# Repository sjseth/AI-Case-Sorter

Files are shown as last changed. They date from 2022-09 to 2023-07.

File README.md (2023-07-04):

# Important: This version of the project has been "retired"

## If you are thinking of starting on this project, please go to the latest version of the project CS7.1 Repo and start with the Instructions.pdf file. 

[CS7.1 Repo](https://github.com/sjseth/AI-Case-Sorter-CS7.1)

[CS7.1 Instructions](https://github.com/sjseth/AI-Case-Sorter-CS7.1/blob/12b74c1f0a16aa015d7ec6fccc47490c912a801d/Instructions.pdf)

# 
#

# AI-Case-Sorter ARCHIVE
This project contains the assets and resources for creating the AI Case sorter project as seen at: https://youtu.be/KBhd5qHZM7I

# Build Videos
[Sorter Construction Part 1][costruciotn1]

[Sorter Construction Part 2][costruciotn2]

[Sorter Construction Part 3][costruciotn3]

[Sorter Construcion Part 4][costruciotn4]

# CS7
[CS7 Concept Video][CS7-Concept]

[CS7 version update video][CS7-accouncement]

# Mods

[Strip-light Mod][light_mod]

[308 shell plate (requires CS7 "Tall" lid)][308_mod]

# Software
The software for this project can be found at: https://www.reloadingrecipes.com/

[Primer size sorting software update video][primer_update]

[costruciotn1]: <https://youtu.be/-Nw5cI27Rd8>
[costruciotn2]: <https://youtu.be/JH8qHSnzCFk>
[costruciotn3]: <https://youtu.be/LoM94kZkPA0>
[costruciotn4]: <https://youtu.be/fzv0i5LFrfs>

[CS7-Concept]: <https://youtu.be/BHhbmp4SDM4>
[CS7-accouncement]: <https://youtu.be/GTHugpKRd10>

[light_mod]: <https://youtu.be/j714uOy7tMQ>
[308_mod]: <https://youtu.be/jFpyLU6bnjw>

[primer_update]: <https://youtu.be/vlp6HSuLg_o>

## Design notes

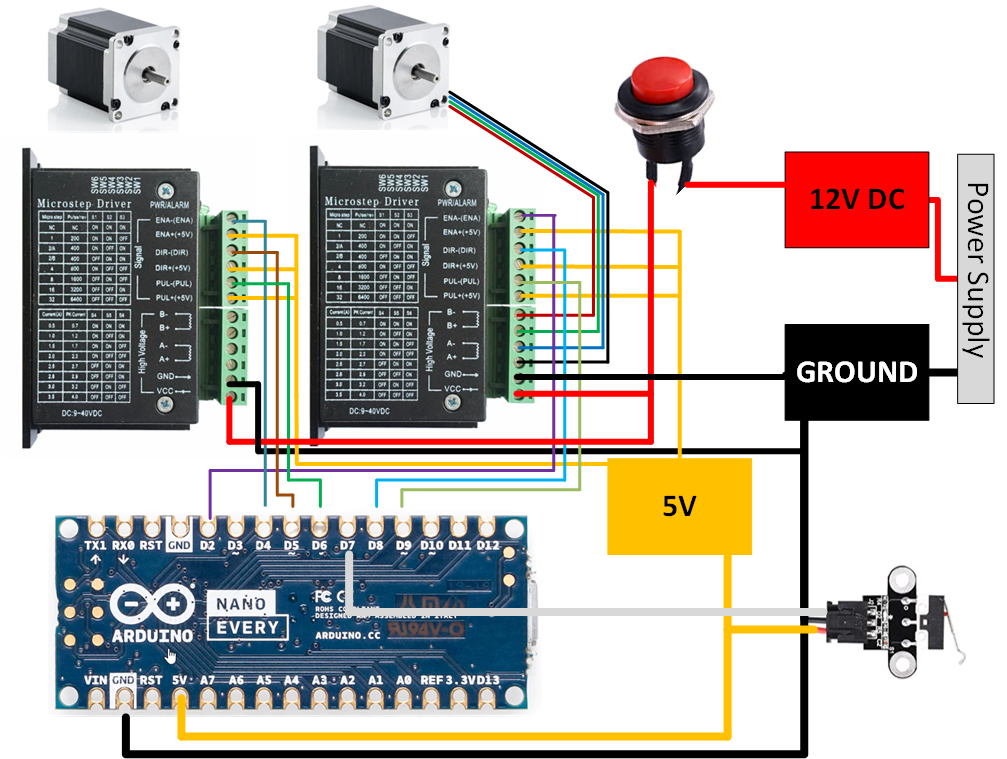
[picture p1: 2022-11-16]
Arduino/Case_Sorter_Schematic.png

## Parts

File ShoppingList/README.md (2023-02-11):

# AI-Case-Sorter

(2) [Nema17 Stepper Motors 1.5A](https://www.amazon.com/STEPPERONLINE-Stepper-63-74oz-Connector-Extruder/dp/B07LF898KN)

(1) [Arduino Nano](https://www.amazon.com/DWEII-ATmega328P-Compatible-Arduino-Unsoldered/dp/B09VKTPPZR)

(2) [TB6600 Stepper Controllers](https://www.amazon.com/UsongShine-Stepper-Controller-Arduino-Printer/dp/B07HHS14VQ)

(1) [ELP VGA Super Mini VGA USB Camera Module 100deg](https://www.amazon.com/dp/B01DRG250Q)

(1) [White LED String Light](https://www.amazon.com/Waterproof-Operated-Decoration-Christmas-Holiday/dp/B01837ULSC)
OR
(1) [White 4000k LED Strip Light (BETTER)](https://www.amazon.com/gp/product/B08X1LK54Z)

(1) [4K ohm resistor](https://www.amazon.com/dp/B0185FHL30)

(1) [Threaded Insert Kit](https://www.amazon.com/Hilitchi-Threaded-Embedment-Printing-Assortment/dp/B08Z86Z85R)

Alternatively, you can use buy just the sized you need:
-  [m3x6x5](https://www.amazon.com/Hilitchi-Threaded-Embedment-Printing-Assortment/dp/B08Z89R4HP)
-  [m5x8x7](https://www.amazon.com/Hilitchi-Threaded-Embedment-Printing-Assortment/dp/B08Z89Q6F7)

(1) [M3 M4 M5 flat head kit](https://www.amazon.com/gp/product/B077ZWV6T2)
or: 
- (4) m3x12 flat head
- (8) m3x16 flat head
- (4) m4x20 hex socket 
- (4) M3x16 hex socket

(1) [M6 hex nut kit ](https://www.amazon.com/M6-1-0-Stainless-Thread-Bright-Finish/dp/B08Y8PV88V/)
 
(1) [5mm Flange Shaft Coupling](https://www.amazon.com/gp/product/B07L1FMBBC)
(1) [Assorted spring kit](https://www.amazon.com/gp/product/B076XKY3JM)
or: 
- (1) 5.55x25.4 extension spring
- (1) 9.1x34.9 compression spring

(1) [Micro Limit Switch (homing sensor)](https://www.amazon.com/gp/product/B07PCN6T6F)

(1) [12v 5amp Power Supply](https://www.amazon.com/gp/product/B01GEA8PQA)

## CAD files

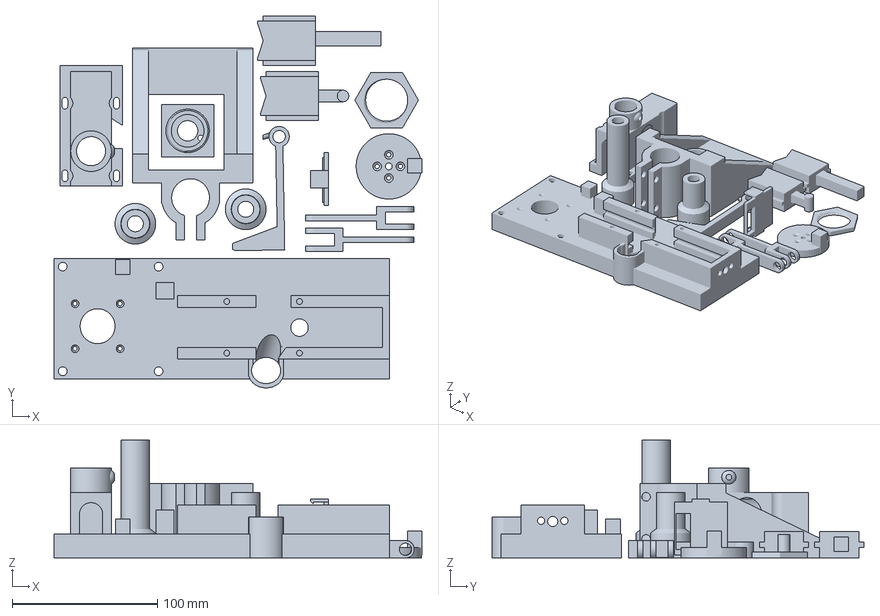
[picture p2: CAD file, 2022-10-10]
3D Printed Modules/1 - Classifier/CS6/CFFFP_CS6_Complete.3mf
253.3 x 256.0 x 81.0 mm

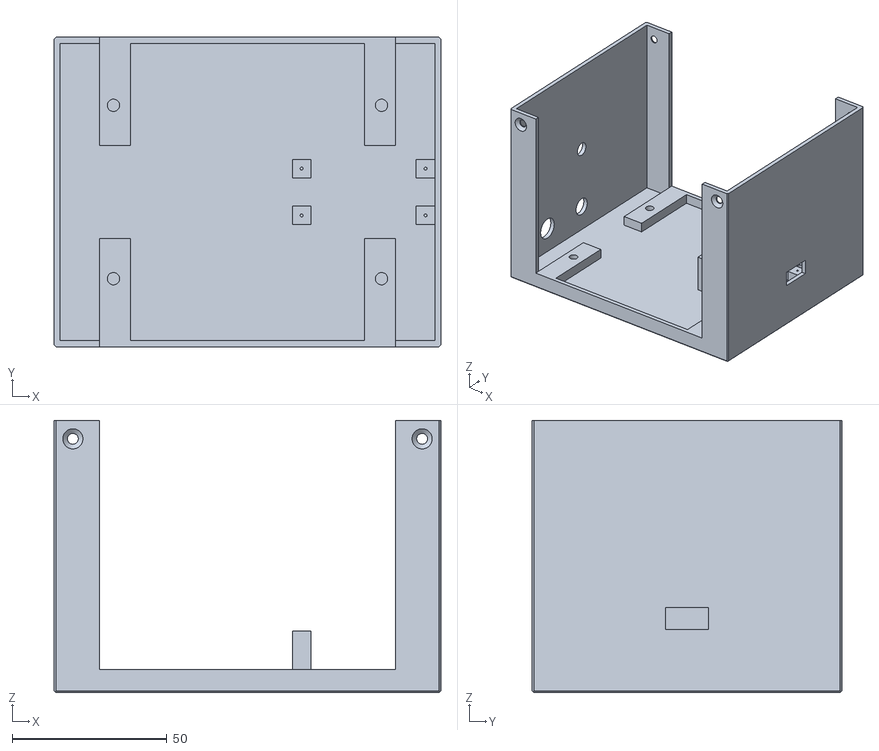
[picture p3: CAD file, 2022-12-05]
3D Printed Modules/3 - Electronics Housing/Experimental/CS7 - Nano + TB6600 Electronics Main.stl
125.0 x 100.0 x 88.0

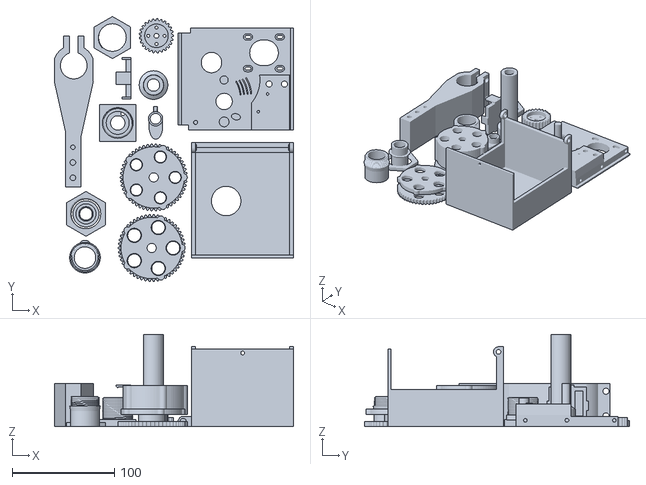
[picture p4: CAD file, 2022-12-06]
3D Printed Modules/1 - Classifier/CS7/CS7_Classifier_Complete.stl
234.0 x 259.0 x 90.0

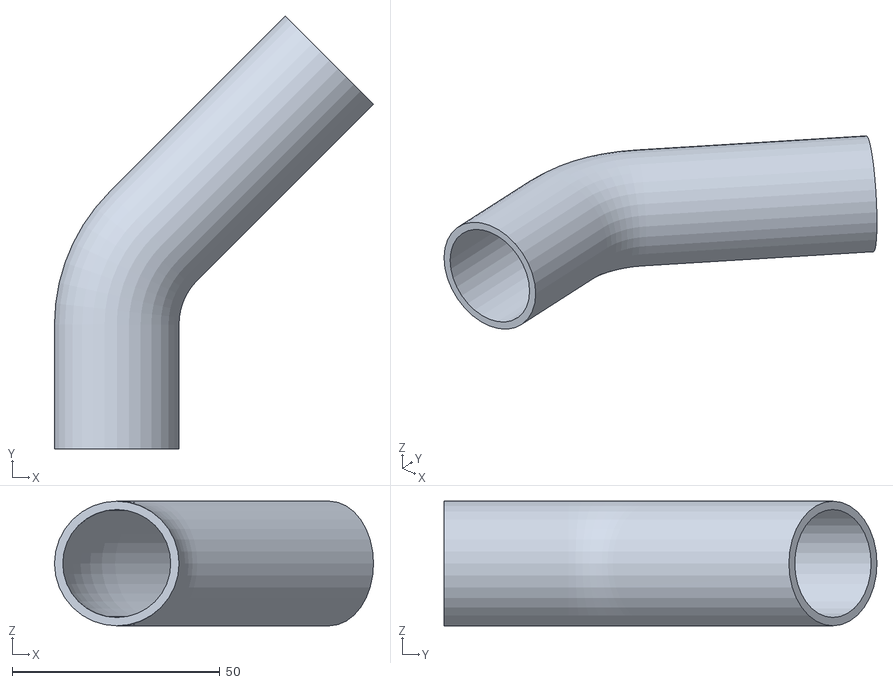
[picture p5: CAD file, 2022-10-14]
3D Printed Modules/2 - Sorter/FeedPipeMain.stl
76.8 x 104.2 x 30.0

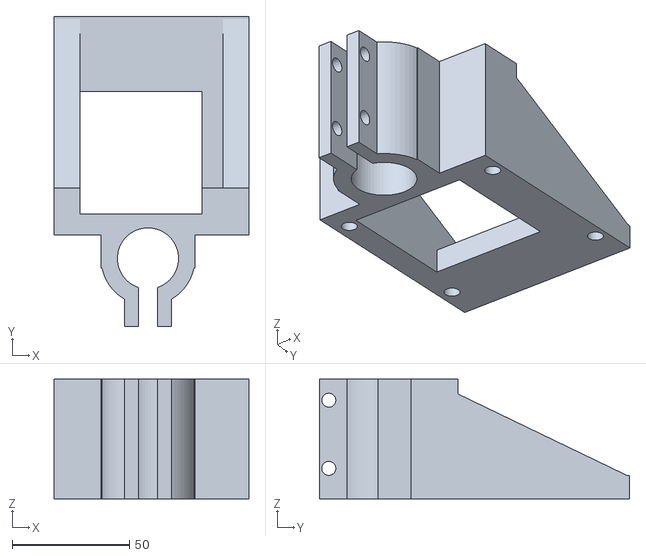
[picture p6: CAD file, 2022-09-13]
3D Printed Modules/1 - Classifier/CS6/CS6_MainBodyPoleMount.stl
83.0 x 132.0 x 51.0

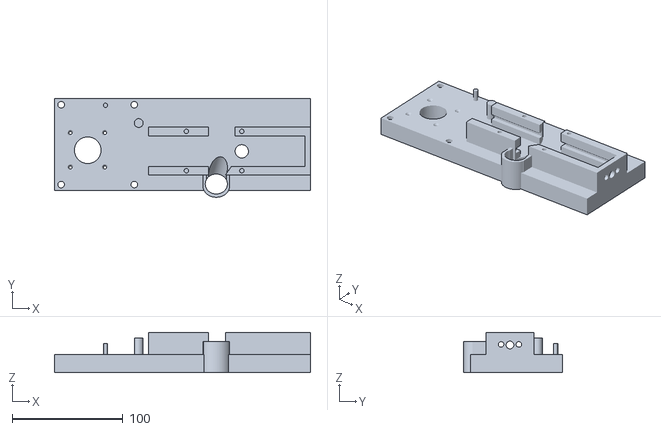
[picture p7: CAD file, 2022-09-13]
3D Printed Modules/1 - Classifier/CS6/CS6_MachineMainBody.stl
231.0 x 89.0 x 36.5

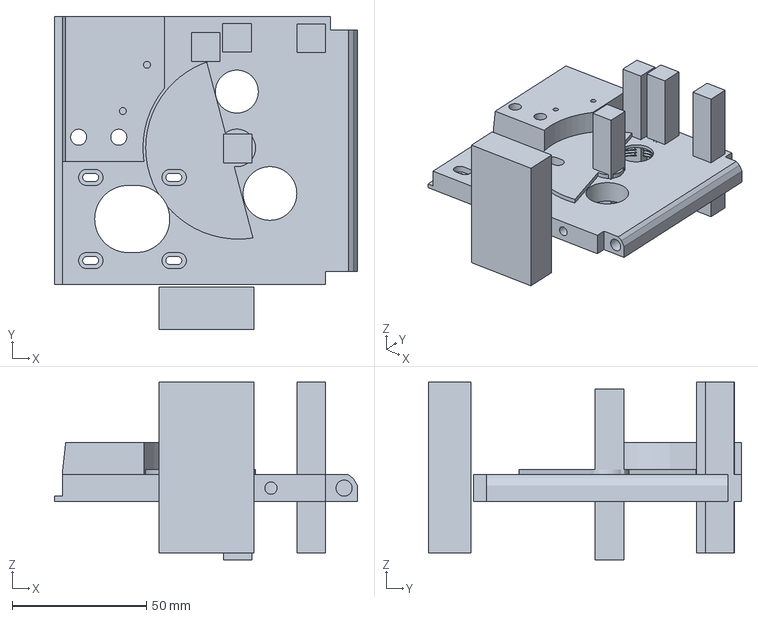
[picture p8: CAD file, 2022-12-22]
3D Printed Modules/0 - Camera/Experimental/CFFFP_CS7 - Sorter Base Exp.3mf
113.0 x 116.7 x 66.3 mm
CS7 - Sorter Base Exp.stl
CS7 - Tension Cam Extended w oRing.stl

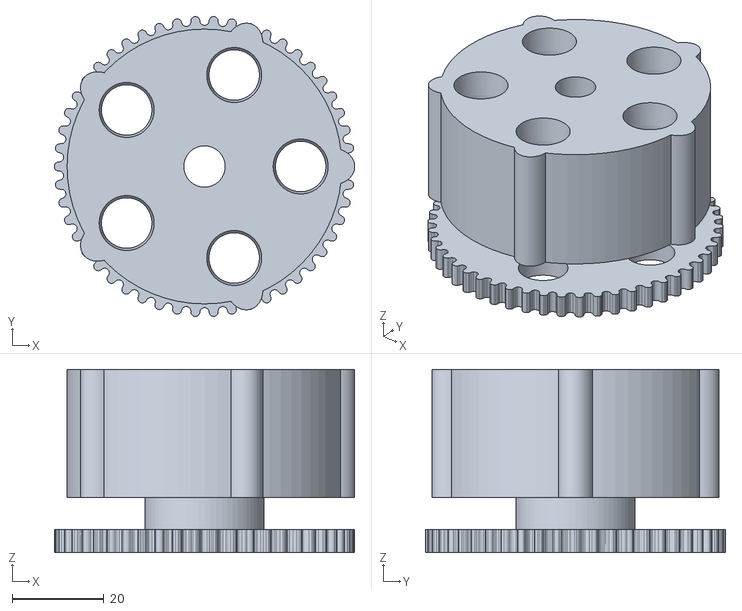
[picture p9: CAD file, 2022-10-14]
3D Printed Modules/1 - Classifier/CS7/Caliber Specific Parts/223-556/CS7_223-556-IndexWheel.stl
65.6 x 65.5 x 40.0

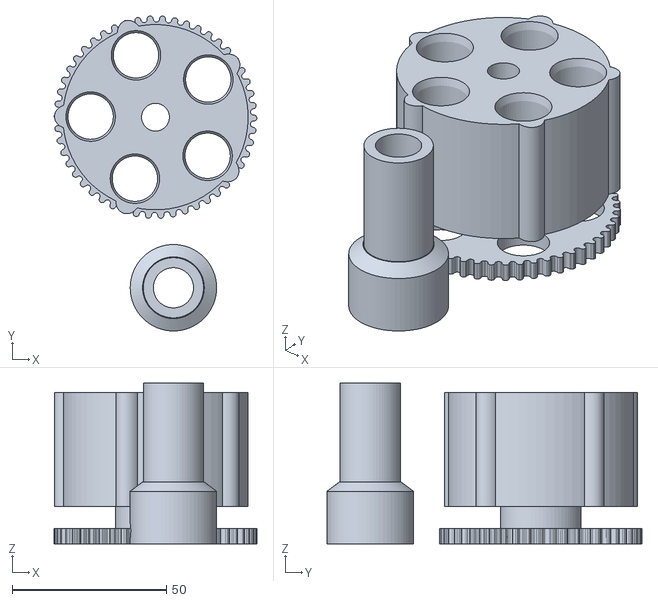
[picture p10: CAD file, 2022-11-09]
3D Printed Modules/1 - Classifier/CS7/Caliber Specific Parts/308/CS7-308-Conversion.stl
65.6 x 102.0 x 52.0

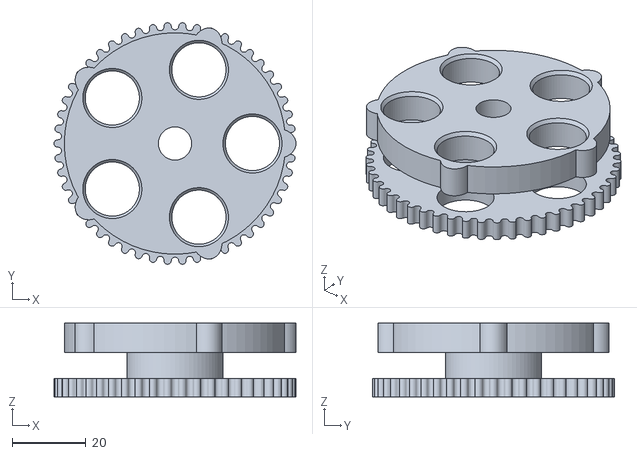
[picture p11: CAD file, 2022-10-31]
3D Printed Modules/1 - Classifier/CS7/Caliber Specific Parts/45AUTO/CS7-Wheel-45AUTO.stl
65.6 x 65.5 x 20.0

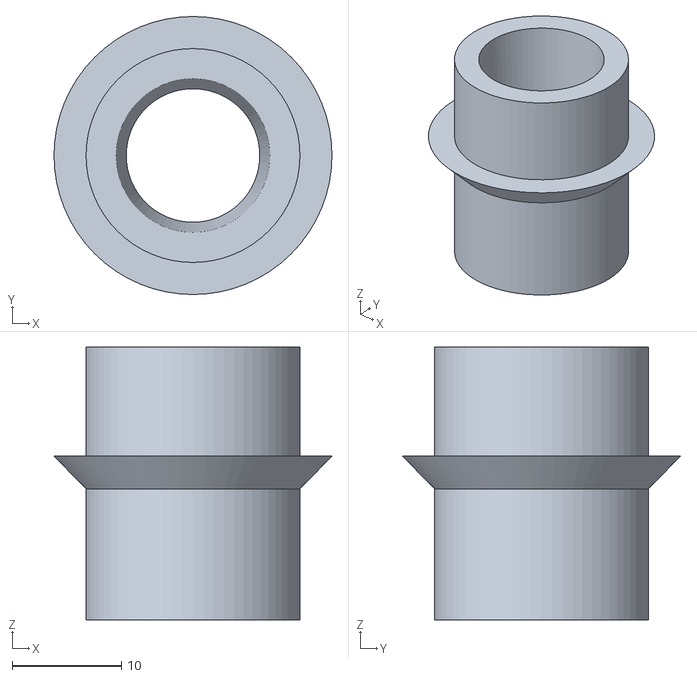
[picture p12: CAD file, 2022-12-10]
3D Printed Modules/1 - Classifier/CS7/Caliber Specific Parts/9mm/CS7 - 9mm Drop Nozzle.stl
25.5 x 25.5 x 25.0

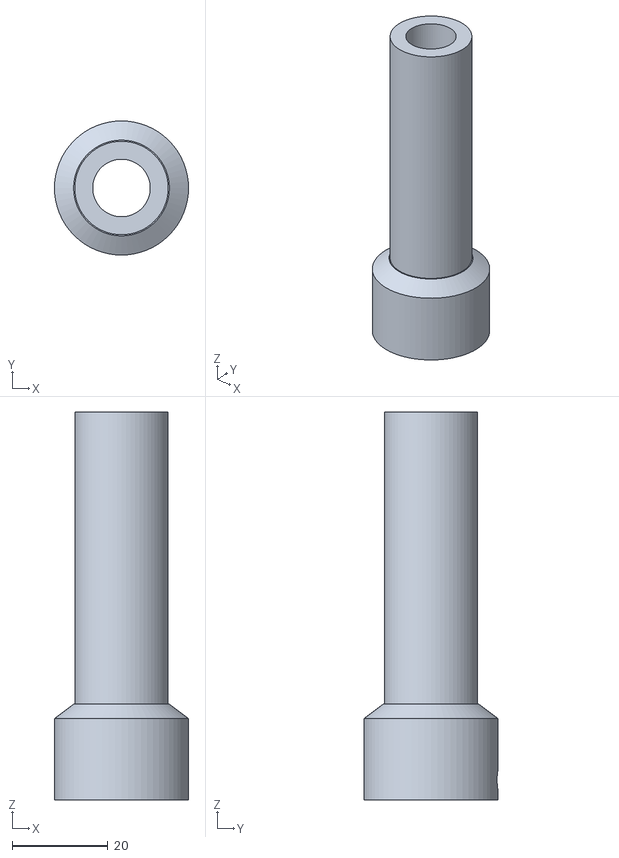
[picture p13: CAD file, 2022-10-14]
3D Printed Modules/1 - Classifier/CS7/Caliber Specific Parts/CS7_FeedNozzle.stl
28.0 x 28.0 x 81.0

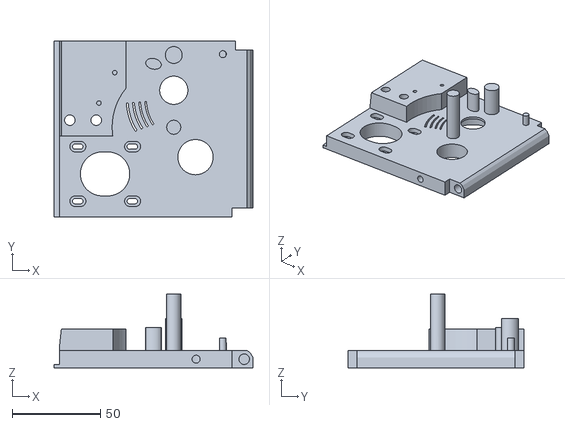
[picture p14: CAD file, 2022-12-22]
3D Printed Modules/1 - Classifier/CS7/Experimental/AirShield/CS7_1 Blackbox Base.stl
113.0 x 100.0 x 42.0

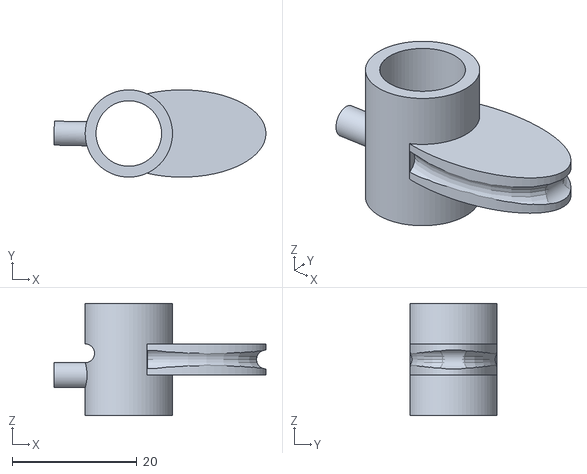
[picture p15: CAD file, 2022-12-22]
3D Printed Modules/1 - Classifier/CS7/Experimental/CS7 - Tension Cam Extended w oRing.stl
34.0 x 14.0 x 18.0

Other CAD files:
3D Printed Modules/1 - Classifier/CS6/CS6_Complete.stl
3D Printed Modules/2 - Sorter/CS5/CS5_PVC_PLATE.stl
3D Printed Modules/2 - Sorter/CS6/Sorter_Arm.stl
3D Printed Modules/2 - Sorter/CS7/27_5mm Mount -IronPipe/Sorter Minimal Mount_27mm.stl
3D Printed Modules/0 - Camera/CS5_CameraModule_lid.stl
3D Printed Modules/0 - Camera/CS5_LightRing.stl
3D Printed Modules/0 - Camera/CS6_CameraModule_Body.stl
3D Printed Modules/0 - Camera/CS7_Camera_Nut.stl
3D Printed Modules/0 - Camera/Experimental/CS7 Camera v2.stl
3D Printed Modules/0 - Camera/Experimental/CS7_1_BlackboxBase.3mf
3D Printed Modules/1 - Classifier/CS6/CS6_223FeedPiston.stl
3D Printed Modules/1 - Classifier/CS6/CS6_9mmFeedFunnel.stl
3D Printed Modules/1 - Classifier/CS6/CS6_Con-rod.stl
3D Printed Modules/1 - Classifier/CS6/CS6_Ejector.stl
3D Printed Modules/1 - Classifier/CS6/CS6_FeedBed_ShortVersion.stl
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

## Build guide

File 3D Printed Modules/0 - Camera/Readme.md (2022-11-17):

# Camera Module
The Camera Module consists of 4 parts:

## The Camera
The cameras is a USB camera module with a 100 degree lense, be sure you purchase the 100 degree lense variant as other lenses have not been tested and this will reduce compatability of AI training sets between your build and other peoples. 

[Source from Amazon.com][Amazon-link]

[Source from Ali Express][Aliexpress-link]

## Camera Body 
Print with supports only touching base and support overhange angle at 80 degrees. This will prevent supports from getting in the threads. 
If using Cura Slicer, use these support settings: 

* Support Structure: Normal,  
* Support Placement: Touching Buildplate, 
* Support Overhang Angle: 80.0, 
* Support Wall Line count: 0

## Camera Nut
This should be placed flat on the build plate and printed without supports. 

## Camera Module Lid
Should be printed with the flat part down with supports on to suport the clips. 
If you are getting breakage at the clips or poor layer adhesion, you can print this part on its side with supports for greater strength. 
Recommend use of PLA+ for this part. 

[Amazon-link]: <https://www.amazon.com/dp/B01DRG250Qdcwxa>

[Aliexpress-link]: <https://www.aliexpress.com/item/4000614474904.html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"sku_id"%3A"10000004016284977"%7D&pdp_npi=2%40dis%21NOK%21263.94%21250.77%21%21%2192.79%21%21%402101e9d316664697050524419e75a3%2110000004016284977%21sea&curPageLogUid=ZHqutjEPQrzU>

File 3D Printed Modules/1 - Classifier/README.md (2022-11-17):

# Classifier
The classifier takes in brass via the feed nozzel, Imaged it using the camera module and drops it out the drop nozzle. 

It is reccomended that the classifier is built as the second module of the build so that you can build your training set while the sorting module is printing. 

It is reccomended that anyone starting with this project does so using the CS7 build

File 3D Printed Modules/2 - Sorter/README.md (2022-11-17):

# Sorter
The sorter rotates a feed pipe to sort cases into one of many bins by rotating the to the appropriate bin prior to the classifier dropping the case.

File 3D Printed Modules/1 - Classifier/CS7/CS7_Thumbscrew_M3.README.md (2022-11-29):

### Thumbscrew cap created by user: anticolon. 

This is a cap which can be glued to a m3 screw and used as a thumbscrew to replace the existing m3 screw which holds the lid on.

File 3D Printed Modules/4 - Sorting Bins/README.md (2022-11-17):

# Sorting Bins

The sorting bin has an additional spot to hold a slip of paper or cardstock to label the contents of your bin and a hole for hanging the bins that is also helpful in grabbing and moving them about. 

The label holder is sized appropriately to accept a [standard microscope][amazon_miscroscope_slides] slide to keep your labels from getting dirty. 

[amazon_miscroscope_slides]: <https://www.amazon.com/gp/product/B0747R2M26/ref=ppx_yo_dt_b_search_asin_title?ie=UTF8&th=1>

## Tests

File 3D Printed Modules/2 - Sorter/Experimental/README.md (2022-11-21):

# Experimental
Stuff in this folder is in the process of being tested/refined. 

### Sorter Minimal Design
This design eliminates the sorter plate and piping. It features an adjustable motor/sorter arm mount. 
Recommend printing in PLA+ at layer height of .24mm with infill no less than 15%. Supports are required and recommendation is support overhang angle of 80 degrees. 

* SorterMinimalDesign (Includes both sides of mount)
* SorterMinimalDesign_MotorSide (the side which motor attaches to)
* SorterMinimalDesign_PoleSide (the side which attaches to the pole)

### Here is an example of what it looks like:
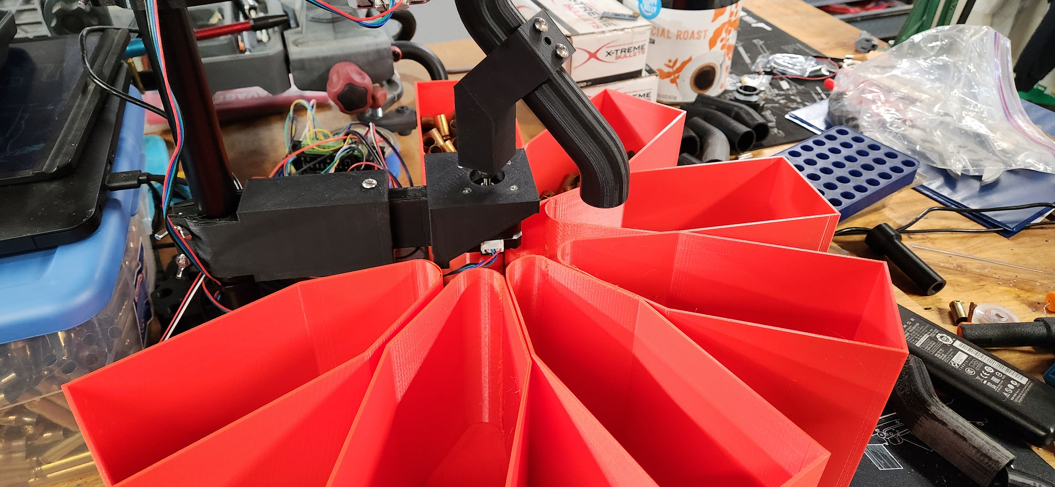
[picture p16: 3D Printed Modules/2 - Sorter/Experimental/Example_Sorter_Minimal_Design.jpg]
SorterMinimalDesign


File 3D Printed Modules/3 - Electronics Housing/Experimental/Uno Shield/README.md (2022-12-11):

### Electronics housing for Arduino Uno with motor shield

Here is the parts list for this enclosure

* [40mm Fan](https://www.amazon.com/dp/B07CH6YC32)
* [CNC Shield Expansion Board V3.0 +UNO R3 Board + A4988 Stepper](https://www.amazon.com/dp/B06XHKSVTG)
* [5.5 x 2.5mm DC-099 DC Jack](https://www.amazon.com/outstanding-5-Pack-Threaded-Connector-Adapter/dp/B07C4F7BP5)
* [SPST Latching Type Push Button](https://www.amazon.com/gp/product/B06XF6PT9L)

The code for the Arduino Uno with motor shield is here:

[Uno with MotorShield Code ](../../../../Arduino/case_sorter_CS7_UNOSHIELD)

# Other Resources

* [Link to CNC Shield Manual](https://www.zyltech.com/arduino-cnc-shield-instructions/)
* [2.54mm Connector Kit](https://www.amazon.com/Glarks-Connector-Housing-Compatible-Assortment/dp/B07CTHCG5T)
* [2.54 Crimper tool](https://www.amazon.com/gp/product/B088NQV8Z3)

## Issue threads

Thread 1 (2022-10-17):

Camera module

xaybiz, 2022-10-17:
Hi
First of all thank you for sharing this fun project!

I have a question regarding the camera module. The seller on Amazon doesn’t seem to ship to Europe (or at least to my country). Do you know another link from for example Aliexpress for a camera that would work? I’m having trouble finding the correct size.

Kokken76, 2022-10-22:
This seems to be the same
https://www.aliexpress.com/item/4000614474904.html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"sku_id"%3A"10000004016284977"%7D&pdp_npi=2%40dis%21NOK%21263.94%21250.77%21%21%2192.79%21%21%402101e9d316664697050524419e75a3%2110000004016284977%21sea&curPageLogUid=ZHqutjEPQrzU

sjseth, 2022-10-23:
Yes, it appears to be...and at a lower price if you are willing to wait

Sent from my Verizon, Samsung Galaxy smartphone

-------- Original message --------
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

xaybiz, 2022-10-23:
Thanks! I actually found and bought it yesterday. I was going to update here but you beat me to it.

It’s either waiting 1-2 months for this camera or modifying the camera housing to fit other circuit board size. I was being lazy this time since I’m not in a hurry.

Closed 2022-11-29.

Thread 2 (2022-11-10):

Separate Objects within .STL files

osteth, 2022-11-10:
Hey! This projects if very cool. I recently ran into an issue printing out the CS7 base.
Within the following file:
[AI-Case-Sorter](https://github.com/sjseth/AI-Case-Sorter)/[3dModels](https://github.com/sjseth/AI-Case-
Sorter/tree/main/3dModels)/[CS7](https://github.com/sjseth/AI-Case-Sorter/tree/main/3dModels/CS7)/CS7_BlackBox_Base_wSensor.stl

The drop nozzle is floating above the build plate so that it is printed in mid-air causing the print to fail.
This specific issue highlights the fact that multiple .stl files have multiple parts combined in the same file. This makes it very difficult to orient and print each part appropriately as well as causing difficulty reprinting any combined part that fails to print properly.

If you are able to break them out in your cad program into individul components per .stl file It would be appreciated. I am currenty addressing the issue adding negative build volume in prusa slicer to make the other parts not print and its not a great work arround.

sjseth, 2022-11-11:
Thanks for letting me know. I will have a look and fix.

________________________________
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

sjseth, 2022-11-11:
Hi Seth,

I have updated the models to fix the issue. Actually I removed that model as it wasn't supposed to go to the repo.

The latest version of the base is here:
https://github.com/sjseth/AI-Case-Sorter/blob/main/3dModels/CS7/CS7_BlackBox_Base.stl

Also the nozzle is separate now as well:
https://github.com/sjseth/AI-Case-Sorter/blob/main/3dModels/CS7/CS7_9mm_nozzle.stl

Cheers!

________________________________
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

osteth, 2022-11-16:
No problem,  I did have a similar but different issue with
https://github.com/sjseth/AI-Case-Sorter/blob/main/3dModels/CS7/CS7_CameraParts.stl
I wanted to print the camera backing with support for the clips. but I couldn't manage to remove the support material without destroying the threads of the other two parts. wasn't a particularly large hurdle. I just turned on supports and placed a support exclusion on the treaded parts and that got me there. but breaking them apart could be useful.

Closed 2022-11-16.

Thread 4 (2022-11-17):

Electronics Enclosure Lid??

osteth, 2022-11-17:
Is there a lid for the electronics enclosure? I couldn't find one.

sjseth, 2022-11-17:
Currently there is no lid. The enclosure needs to be redesigned. It has several issues which need to be addressed. I have a few experiments to complete with other controllers before I spend more time on the enclosure.  Not sure if I want to stay with the tb6600 as there are better options out there

Sent from my Verizon, Samsung Galaxy smartphone

-------- Original message --------
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

osteth, 2022-11-17:
ok cool.
It might be worth taking a look at something like these low cost modules. they would significantly reduce the build cost if they are sufficient.
https://www.amazon.com/Expansion-Stepper-Drivers-Arduino-Printer/dp/B07LH5XTCL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

Closed 2022-11-22.

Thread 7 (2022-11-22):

Motor Driver dimensional tollerances.

osteth, 2022-11-22:
I got in a motor driver today that is too large for the enclosure. I purchased from the provided link. but it appears that they don't have terribly tight tolerances on the heat sink extrusions.

The ones I received measured out to 118.5mm so they will not fit in between the enclosure walls. I just wanted to make a note of it because there appears to be some variability even from the same vendor.

sjseth, 2022-11-29:
Ok, thanks for the info. I am leaving this open for now as I am working on a new electronics package / enclosure which I think will be much better than the current existing setup which uses the tb6600.

osteth, 2022-11-30:
Now I see where the package size issue I am having came from. They sent me DM556 drivers instead of tb6600 even though I ordered off the tb6600 link in the shopping list.

Alphadawg0024, 2023-02-27:
Do you have an updated link to the Discord server. Jumping into this project but the Discord link expired

sjseth, 2023-02-27:
Please email me directly for that.  I don't want to publish links here.

Email is in the about page here:

***@***.***/about

________________________________
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

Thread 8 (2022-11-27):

CS7_Camera_Nut.stl size

Mograthi, 2022-11-27:
The CS7_Camera_Nut.stl is importing into slicers as a giant object 379.6 x 438.3 x 40 mm

osteth, 2022-11-28:
That one is on me. I tried to isolate the nut from the rest of the parts without the original cad file and something went wrong apparently ( I am assuming that it was a unit conversion issue)
Please use this file until I can figure it out.
https://github.com/sjseth/AI-Case-Sorter/blob/a3689c34340b883cd53d27106b8b8bb5844e6180/3dModels/CS7/CS7_CameraParts.stl5

osteth, 2022-11-28:
The issue should be rectified in my pull request. (https://github.com/sjseth/AI-Case-Sorter/pull/9)
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

sjseth, 2022-11-29:
Thanks for the quick fix.  Verified that the issue has been resolved.

Closed 2022-11-29.

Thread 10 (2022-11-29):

Thumbscrew for the lid and droptube.

anticolon, 2022-11-29:
Hey Seth, just found your project the other day on youtube and was thrilled as i've been thinking of designing something along these lines for a while now. I'm printing your design as we speak and have already ordered most of the stuff needed. So big thanks for sharing this project!

Now, to my idea for improvement, in other projects with screws to secure stuff, I've seen people using a hexbolt (screw) and then printing a small thumbpart that fits over the head. This is quite secure when fitted with hotglue. This would minimize the need for tools when doing caliber change.

Best regards
Karl

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

anticolon, 2022-11-29:
I'll try to add an STL for a similar that I just made.

osteth, 2022-11-29:
The general workflow for making changes to a repo is to make a fork,
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
Then make a branch inside of your fork. (shown using github desktop client https://desktop.github.com/)
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
Then make and commit your changes to your branch
Finally, generate a pull request to allow for them to be reviewed and merged into main.
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

If all else fails you can change the file extension from .stl to .png and upload them in a comment here and I can generate a merge request.

sjseth, 2022-11-29:
Thanks anitcolon for the idea and Seth for the guidance.  The pull request has been merged to the branch and in addition I added a readme file for how the screw is supposed to be used since it requires additional gluing.

anticolon, 2022-11-29:
Turns out, atleast when i print them, they are pressfit. No glueing required.

anticolon, 2022-11-29:
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

Closed 2022-11-29.

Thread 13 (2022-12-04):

Add countersink to motormount on CS7 classifier base.

anticolon, 2022-12-04:
When mounting the motor I needed to drill out some material to countersink the screws so that the indexwheel could move freely.
Would be nice to have it in the model.

sjseth, 2022-12-05:
I am working on this one. thinking of recessing them all and using cap screws. Doing some experiments.

sjseth, 2022-12-06:
Thanks. I have recessed 3mm and tested it and it works with both standard and cap m3 screws.

anticolon, 2022-12-06:
Looks good!

Closed 2022-12-06.

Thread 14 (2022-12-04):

CS7 Classifier drive gear catches indexwheel when rotating.

anticolon, 2022-12-04:
Had to remove some material from the 9mm indexwheel so that the drivegear wouldn't catch when rotating. Maybe the drivegear doesn't have to be that tall, and thus removing the issue?

sjseth, 2022-12-05:
Ok, I have updated the drive gear to shorten it which resolves this issue. Thanks!

Closed 2022-12-05.

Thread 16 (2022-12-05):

Feed Adapter compatible with BF556 Feeder design.

anticolon, 2022-12-05:
Hi Seth,

Could you make a experimental feed adapter with innerdiameter of 16,5mm and make the top lower by 6mm? This would make it plug & play with the LEE APP droptubes in the excellent feeder that BF556 has designed.
https://github.com/BF556/Feeder

Would be much appreciated!

sjseth, 2022-12-05:
Added to the Experimental folder in classifier

anticolon, 2022-12-06:
Thank you! Will print later today for testing.

anticolon, 2022-12-06:
Printed it, and i think it needs 0,5mm more, so could you update it to 17mm inner diameter. Lengthwise it's perfect.

Closed 2022-12-05.

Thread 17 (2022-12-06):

BF556 feed adapter adjustment

anticolon, 2022-12-06:
Don't know if this is the right way to go about changes to a closed issue, but here i go. Correct me if I should have done it some other way. :)

Printed it, and i think it needs 0,5mm more, so could you update it to 17mm inner diameter. Lengthwise it's perfect.

Originally posted by @anticolon in https://github.com/sjseth/AI-Case-Sorter/issues/16#issuecomment-1339792251_

sjseth, 2022-12-06:
I am guessing it is probably related to shrinkage. Can you measure your printed item to see if what the ID is?
If it is not 16.5, you might try scaling it up by 1 or 2 percent.

If it did print out exactly at 16.5mm and is too small, I am happy to increase the ID to 17.

________________________________
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

sjseth, 2022-12-07:
Thanks for the update Karl. I have no problem making it bigger and I don't think .5mm will have much effect anyhow, but the original requestor requested it to be  16.5 so I didn't want to mess him up either.  I suspect that for this application 16.5 would be a very tight fit as well as 17mm so I will go ahead and update it.

________________________________
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

sjseth, 2022-12-07:
Sorry, just realized that Karl and Anticolon are 1 in the same... I have updated the part.

anticolon, 2022-12-07:
Hehe, I just added my name to the profile, thought it would be nicer that way. Thanks for updating, I'll print a new one tomorrow and get back to you. Midnight here in Sweden. 😀

anticolon, 2022-12-09:
Printed and verified, works perfectly now that you made the ID 17mm.

Closed 2022-12-07.

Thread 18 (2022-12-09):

Sorter Plate Too Large for My Printer

BigTJohn, 2022-12-09:
When I import the sorter plate.stl into Cura, it says the dimension is too late for my build area. I have an Ender 3 S1 Pro with a build area of 220x220x270. Was sure it would fit. Is there a smaller dimension I can use or do I try to make a wooden sorter plate?

anticolon, 2022-12-09:
That's not right, I'm not used to Cura, but did you import the model with the correct settings. I believe it should be imported with metrics (mm) setting.

BigTJohn, 2022-12-09:
I’m sure I just downloaded the file from SJSETH then just imported it to CURA. I did the same to all the rest of the files and they are good. Some long print times but very good quality. I have only the outer greyed out margins on the print preview left but I don’t think I can use that area. I was sure the file would be just fine however it just is too big for the printer. I don’t know what the physical measurement of the Sorter Plate is, but it would seem it would fit easily
Thanks for getting back, John

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

sjseth, 2022-12-09:
It may be that Cura is accounting for the skirt or brim. If you set the build plate adhesion type to none, it should be fine for your bed size of 220

BigTJohn, 2022-12-11:
This could be the case however, the other items so far have been downloaded and imported to cura, sliced and they print very well. How big is the sorter plate in mm? It just does not make sense it is so large. On your video, it seems no larger than 150-160 mm across. But that’s just a guess on my part. I will try to get it to download again and see what happens.
Thanks, John.

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

sjseth, 2022-12-11:
It is 200mm diameter. There is a minimal sorter 3d model which can be seen in my  latest video which is in the experimental folder. It had a much smaller print area requirement and may work better for you.

https://youtu.be/uEW3m3bBLPA

Sent from my Verizon, Samsung Galaxy smartphone

BigTJohn, 2022-12-11:
You were correct, it was the skirt/brim. Changed that to "none" and it is printing merrily away. Should be done in another 16 hrs or so.
The link listed in the recent video for the taller lid does not come up. I get a "404" not found message and I do not see the tall lid in the print files.
Many thanks for this project, it is proving quite the fun challenge. So far the electronic side coming together. I see the new electronic box (are files available yet?) uses an Arduino UNO instead of the Nano.  Good thing as I have two of them. Now waiting for the motor shield and camera to come in.

sjseth, 2022-12-11:
The tall lid is now the normal lid

https://github.com/sjseth/AI-Case-Sorter/blob/main/3D%20Printed%20Modules/1%20-%20Classifier/CS7/CS7_Classifier_Lid.stl

The new electronics models and info is here:
https://github.com/sjseth/AI-Case-Sorter/tree/main/3D%20Printed%20Modules/3%20-%20Electronics%20Housing/Experimental/Uno%20Shield

Sent from my Verizon, Samsung Galaxy smartphone

-------- Original message --------
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

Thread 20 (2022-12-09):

Arduino Uno Shield Electrical Drawing

BrickSolid28, 2022-12-09:
Does anyone have a basic electrical drawing for the Uno with CNC backpack?  Even a basic picture of a working setup would help.  Are we using a 12V or 24V power source for the shield?  I'm assuming 12V as the specified fan is 12V.

sjseth, 2022-12-10:
I am releasing a video on it tomorrow. Stay tuned.
________________________________
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

sjseth, 2022-12-11:
Hopefully this has the information you need.  https://www.youtube.com/watch?v=uEW3m3bBLPA
Also you can find more info in the  Experimental->Uno Shield folder:

https://github.com/sjseth/AI-Case-Sorter/tree/main/3D%20Printed%20Modules/3%20-%20Electronics%20Housing/Experimental/Uno%20Shield

Closed 2022-12-11.

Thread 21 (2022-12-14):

New Sort Pipes

BigTJohn, 2022-12-14:
The New Sort Pipes, while they print great, I think only one of the non flared pipes is needed but they only print in pairs, one non flared and one flared. Since several flared pipes are needed (up to 10) I cannot seem to break out the pair of pipes for individual printing, Is there a method of doing so?
Thanks, John

sjseth, 2022-12-14:
If i understood you correctly, the pair of flared sort pipes with smaller ID were designed be used only for the moving arm where the flat ends butt together. It was a later design where I got rid of the all the other pipes as the two pipes together drop the brass straight down.

Sent from my Verizon, Samsung Galaxy smartphone

-------- Original message --------
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

BigTJohn, 2022-12-15:
So the newest iteration does not use the sorter plate or the 10 pipes from the plate to the bins. If I am understanding this correctly. So far this has been a very interesting journey. Can’t wait to get it finished.
I am assuming you have the .stl files locked and no one can do much if any changes. I have been able to resize a couple things, the bins and the sorter arm.
Thanks for doing this. It’s great!
John

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

sjseth, 2022-12-15:
You should be able to pull the stl file into almost any CAD program and make changes to it. I don't have the source for the files available at this point in time.

Sent from my Verizon, Samsung Galaxy smartphone

-------- Original message --------
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

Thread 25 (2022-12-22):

Arduino sketch

BigTJohn, 2022-12-22:
Me again. Finally got the camera with air shield to fit the black base. It required a bit of sanding and fitting but it is in place. Working on printing sort bins now. Two are in TPU and are maybe a bit too flexible but not terrible. I will do two more in PLA+ and most likely they will bw better suited.
The Arduino sketch is having a problem when I verify it.

//set feed speed. Values 1-100. Def 60

      if(input.startsWith("feedspeed:")){    RIGHT HERE it will fault the statement "a function-definition is not allowed here before "{" token

         input.replace("feedspeed:","");
         feedSpeed= input.toInt();
          Serial.print("ok\n");

I have tried to check why it's doing this but have been fruitless.
Also the stepper motor shield sketch is showing the TB9600 controllers, not the newer, smaller ones with the CNC shield. Does this make a difference in the operation of the Arduino/shield combo?
At least I'm getting closer and with the 3D prints about done it is actually looking much better. Still a ways to go but so far its been fun.

sjseth, 2022-12-22:
Can you tell me which sketch you were using?

Sent from my Verizon, Samsung Galaxy smartphone

-------- Original message --------
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

sjseth, 2022-12-22:
I just checked and compiled all 3 sketches from the repo and they all are working.  Not sure why you would see the error you are seeing. If you modified the sketch, it is possible you left out a closing bracket or semi colon.

In regards to the Arduino Uno sketch having references to tb6600, this is because this sketch is just an evolution of the previous cs7 sketch and I reused the variable names.  It is a good idea to update the variable names as it is a bit confusing.

BigTJohn, 2022-12-23:
Thanks for the quick reply. I haven’t changed the sketch but I will copy it again and see if something was lost in the copy. I would think it would be an easy thing to find, but I just do not see it.
Good idea about updating the naming things separately for each update in equipment. It’s nice to see everything working and I can pretty much follow on with it.
As far as the new sort pipes, I think just a slight change in the radius of the curves would make all the difference and allow 30.06 brass to pass. I just filed/sanded a little and I have the bigger brass going smoothly.
Have a great Christmas!!

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

BigTJohn, 2022-12-26:
I was using the latest sketch, however I had copied it a few times and it finally was correct and loaded into my Arduino. I don’t have the camera software downloaded yet but soon. I still have some 3D printing to do but it has been pretty chilly (well, for FL downright cold) the past few days but should be good later this week. I still have the case feeder to do so still bunch to do. Any idea how many cases a minute the sorter can do? I’m just trying to get int9o my mind and feeder plans what I should try and plan for as far as feeder capabilities.
Also here’s another thing that popped into my little brain, how much force is applied to the sorter platform (the bottom of the floor plate) when the first few cases fall from the feeder? It appears to take quite a hit until there are 5-6 cases in the feeder tube. Am I over thinking this? Should there be a few bends or maybe some brushes to slow the fall of the cases so the hit is not so hard?
Thanks, John

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

sjseth, 2022-12-26:
I think the max processing rate I have achieved was about 3 per second but that was with some of the setting changed and a few tweaks and a very powerful computer.  That said, I think a normal high-end max processing rate would be approximately 50-60rds per minute. There is a speed control in the run tab of the software to slow it down and I have to use that control or I outrun my feeder.

In regards to the force, it hasn't been a problem. If you are printing with pla or pla+ or something harder, it shouldn't be an issue. I don't have any dents in my base. But one thing to consider is that my drop tube actually has two bends in it so this may dampen it a bit. I think the most force is exhibited when you have a full tube of brass. Even then, with many thousands of of peices through the system, it haven't seen significant wear yet.

I use Black Jayo PLA+ for everything now days as it prints really well for me and doesn't crack/break. I get great adhesion at temp of 222C.
________________________________
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

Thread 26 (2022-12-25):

Notch or bend to make spring more secure?

anticolon, 2022-12-25:
Hey Seth,

Just got my sorter running on christmas day, still working out some kinks, I thought of some improvements that I'll post for your consideriation. I'll make an issue for each one.

Consider a notch or bend to make the spring more secure?
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

anticolon, 2022-12-29:
I put a 4mm hole there and put an insert with a screw.
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

BigTJohn, 2022-12-29:
I like your idea foe the spring attachment. I am using a silicon band to connect to the tension device. Your idea is much better and I’ll be doing this as well.
I drilled a hole for the Allen wrench to tighten the set screw on mine. I also used my Dremel to grind the motor shaft so the gear would sit lower as the flat section of the motor shaft would not let the gear go low enough.
This is proving to be a great project. I shoot mostly rife and the larger cases still fit the .308 sorter cylinder and lid. It will be a while before I can finish it up as my printer is taking a while to print and I just purchased it the end of November. So getting everything setup and learning the printer has been a journey as well.  So far, it has been pretty fun.
John...
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

sjseth, 2022-12-30:
I like this idea as well.  I am currently putting together a bunch of changes and combining them in a  7.1 folder.  I think I may use this idea though after adding the notches on both posts, the spring stays put pretty well. I have also redesigned the tension cam a bit as it now has a groove for an oring around it which gives it better gripping power on the case and also less noise as it slips through to the next cartridge.

sjseth, 2022-12-30:
John, the new gear is nearly half the height and should solve that interference issue. It is available now in the classifier folder

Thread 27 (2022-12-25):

Hole for limitswitch cable routing.

anticolon, 2022-12-25:
Hey Seth,

Consider adding a hole somewhere around here to route the cables from limitswitch, that way we could tie it togehter with the cable coming from the camera and link up with the cable from the motor and have a neat looking cable management. :-)

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

Best regards
Karl

anticolon, 2022-12-29:
I added a hole and also a groove at the motor to be able to torque the motorcoupler in the right height.
Should i fork and add this to the project? (there is still the thread for the camera.
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

sjseth, 2023-02-13:
Hi Karl,

Just wanted to let you know that I have created a Discord server for this project and if you are interested in joining, it would probably be a better place to get support and bounce ideas around with the community. I am in the process of inviting those who I know have already completed or are in the process of building this project.

Here is the link to join if you are interested:

https://discord.gg/HaUTpQhV<https://na01.safelinks.protection.outlook.com/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>

Cheers!

Seth
________________________________
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

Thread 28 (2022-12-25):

Notch or bend to make spring more secure

anticolon, 2022-12-25:
Hey Seth,

As per the other issue posted on the need for a notch or something that makes the spring more secure when running the classifier.

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

Best regards
Karl

sjseth, 2022-12-25:
Good point. Hasn't been an issue for me but wouldn't hurt to have a notch in both posts probably

Sent from my Verizon, Samsung Galaxy smartphone

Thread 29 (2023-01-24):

AI sorter download and run

BigTJohn, 2023-01-24:
Hey Seth,
Me again...
I am having trouble getting to the program to run the AI sorter. It downloads from your reloadingrecipes web page but even after I tell MS it is a trusted site, it lists the download as "unconfirmed program" and has a strange file name to it with no (.exe) or other file to run it. Is this an auto executable or is some other program needed. I did download the C++ needed and that shows as no problem. Granted I have not used Win 10 very much, but I don't think it has changed much from the last time I used it.
Clicking on the download does nothing (I now have three copies of it). When you get a chance, let me know what else I need to do if you could.
I do have the complete sorter built and it looks pretty good but there are a couple of adjustments to make everything line up
Thanks, John

sjseth, 2023-01-24:
Usually that "unconfirmed program" is seen when the file is still  in process of downloading or Microsoft Defender is scanning.  It could also be some other AV software is messing with it.  If you right-click on the msi installer and go to the properties, there is a checkbox sometimes named "unblock" which you have to check to override the windows defender block. After unblocking it, you should be able to run the installer.

Also check the size of the download, it should be around 106MB in size.

[cid:5f94124d-ee20-48a9-8ffe-f6bc33a0c525]

Also check the digital signature and make sure you are getting a signed file:
[cid:49394ca6-5075-4fb9-8e10-315b35cb1223]

If those look ok, then go ahead and double click it.. You should get something like this: (even I do and I made the software!)
Click the more info link
[cid:82944460-fefa-47bc-b69d-0bf6ee08640b]

[cid:4d1b3c44-b350-48e6-bfea-78fa544bfb0a]

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

BigTJohn, 2023-01-30:
OK, I have told MS the file is known and trusted. It's still shows unconfirmed, even after allowing it to remain open for several hours. I have tried its on two different computers, same problem. Both of them are running up to date WIN 10.  Also, when I run the second program, it will start and show a "repair, install" box and do nothing. When I click run, it says I have to restart the computer. I restart and see nothing, the AI installer does nothing. So far, I have not been able to figure this out. I have plenty of hard drive space and ram. The AI shows as 106 mb but still with the unconfirmed. I have tried everything I can think of, do you have any ideas?
Thanks. I know I am being a bit of a pest, but this is a great project and I want to see it through to completion.
Thanks for any help. John

sjseth, 2023-01-30:
Perhaps you can try the download from a different computer and put it on a usb thumbdrive and transfer it over that way? Would be curious to see how the file is treated in this manner.
________________________________
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

BigTJohn, 2023-03-03:
I finally have the system (mostly) together and running. The motors are getting power, as they do energize and are hard to turn manually. The AI Sorter (I am using the newest version, 1.0.15.0) is almost working with the following exceptions:
1. No advance of the turret using the feed button. Nothing.
2. No movement of the sorter pipe using the test button. Nothing.
3. The camera image is just OK in the large image. It is about a 1/2 image, only the right half of the image shows to the right of the 8 rotations.
4. The primer mask button does nothing, no masking of the primer.
The Arduino code seems to be functional as the stepper motors power on and are hard to turn manually yet spin easily when Arduino is off. I am using the latest Arduino code.
I have machine 90% done and I am hoping to complete it and start using it. Thanks for any insight you may have, John.

sjseth, 2023-03-04:
Hi John,

You can use the Arduino Serial Monitor Console to ensure the arduino is configured correctly.

When loading the console, you can send commands  like  "0" or any number between 1-8 and it should cycle the feed motor one position.
there is a one command lag between the sort motor, so if you send a 1 followed by a 2, the sorter will move to the 1 slot. if you then send a 5 the sorter will move to the 2 slot.

Please also make sure you have uploaded the latest arduino code from the repo to your arduino device..

There is also a discord group with a bunch of really great guys who have built or are building the project and are really quick to offer assistance. Here is the link to join that group if you are interested:

https://discord.gg/wnv2HBK8
Join the SJSeth's AI Sorter Group Discord Server!<https://discord.gg/wnv2HBK8>
Check out the SJSeth's AI Sorter Group community on Discord - hang out with 25 other members and enjoy free voice and text chat.
discord.gg

________________________________
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

Closed 2023-02-13.

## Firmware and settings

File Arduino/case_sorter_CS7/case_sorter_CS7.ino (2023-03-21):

/// VERSION CS 7.0.230321.2-N ///


#include <Wire.h>
#include <SoftwareSerial.h>

//sends 5v to stepper enable, pul and dir pins if unable to use 5v pin on  arduino
#define TBPOWERPIN 10

//TB6600 PINS (STEPPIN IS PUL- ON TB6000)
//Stepper controller is set to 32 Microsteps

#define FEED_DIRPIN 8
#define FEED_STEPPIN 9  
#define FEED_Enable 2
#define FEED_MICROSTEPS 32
#define FEED_SENSOR 11 //the proximity sensor under the feed tube
#define FEED_HOMING_SENSOR 7  
#define FEED_DONE_SIGNAL 12   // Writes HIGH Signal When Feed is done
#define FEEDSENSOR_ENABLED false   //enabled if feedsensor is installed and working;//this is a proximity sensor under the feed tube which tells us a case has dropped completely

#define SORT_MICROSTEPS 32 
#define SORT_DIRPIN 5
#define SORT_STEPPIN 6
#define SORT_Enable 4
#define SORT_HOMING_SENSOR 14

#define SORTER_CHUTE_SEPERATION 20 //number of steps between chutes
#define QUEUE_LENGTH 2              //usually 1 but it is the positional distance between your camera and the sorter.
#define PRINT_QUEUEINFO false       //used for debugging in serial monitor. prints queue info


/// DELAY SETTINGS ///
//These settings will add delay on feed complete. They are cumulative. These are to help prevent brass slinging
int feedDoneSignalTime = 30;  //The amount of time in MS to send the feed done signal;
int slotDropDelay = 150; //how long to wait before moving the sorter arm after feedcycle has finished. (used to eliminate brass slinging) 

/// FEED SETTINGS ///
bool homeFeedOnStartup = true; //automatically home the feeder on startup
bool autoFeedHoming = true;  //if true, then homing will be checked and adjusted on each feed cycle. Requires homing sensor.
int homingFeedOffset = 2; // the number of steps to continue moving after homing sensor is triggered
int feedSpeed = 90;  //range: 1..100
int feedSteps = 60;  //range 1..1000

/// SORT SETTINGS///
bool homeSorterOnStartup = false; //automatically home the sorter on startup
bool autoSorterHoming = false; //set to true if homing sensor is installed and connected. 
int homingSortOffset = 0; //the amount of  steps to move forward after activating the homing switch
int sortSpeed = 90;     //range: 1..100
int sortSteps = 20;     //range: 1..500 //20 default


//acceleration settings for sorter motor
bool useAcceleration = true;
int upslope = 2 * SORT_MICROSTEPS;
int downslope = 2 * SORT_MICROSTEPS;
int accelerationFactor = 1400;              //the top delay value when ramping. somewhere between 1000 and 2000 seems to work well.
int rampFactor = accelerationFactor / 100;  //the ramp delay microseconds to add/remove per step; should be roughly accelerationfactor / 50
int sortTestDelay = 150;                    //stop delay time in between sorts in test mode
//end acceleration settins


//for the CS7 and CS7.1 the queue length is 2. 
//This is because there are two feeds required to move brass from the camera  to the sorter drop
int sorterQueue[QUEUE_LENGTH];

//not used but could be if you wanted to specify exact positions.
//referenced in the commented out code in the runsorter method below
//int sorterChutes[] ={0,17, 33, 49, 66, 83, 99, 116, 132};


//tracking variables, do not edit!
int sorterMotorCurrentPosition = 0;
bool isHomed = true;
int sorterMotorSpeed = 500;  //this is default and calculated at runtime. do not change this value
int feedMotorSpeed = 500;    //this is default and calculated at runtime. do not change this value
int pulsewidth = 10;  //this is used by both feed and sort motors to set the pulse width in micro seconds.
bool useFeedSensor = FEEDSENSOR_ENABLED;


void setup() {
  Serial.begin(9600);

  setSorterMotorSpeed(sortSpeed);
  setFeedMotorSpeed(feedSpeed);

  pinMode(TBPOWERPIN, OUTPUT);
  pinMode(FEED_Enable, OUTPUT);
  pinMode(SORT_Enable, OUTPUT);
  pinMode(FEED_DIRPIN, OUTPUT);
  pinMode(FEED_STEPPIN, OUTPUT);
  pinMode(SORT_DIRPIN, OUTPUT);
  pinMode(SORT_STEPPIN, OUTPUT);

  pinMode(FEED_DONE_SIGNAL, OUTPUT);
  pinMode(TBPOWERPIN, OUTPUT);

  pinMode(FEED_HOMING_SENSOR, INPUT);
  pinMode(SORT_HOMING_SENSOR, INPUT);
  pinMode(FEED_SENSOR, INPUT);


  digitalWrite(FEED_Enable, HIGH);
  digitalWrite(SORT_Enable, HIGH);
  digitalWrite(FEED_DIRPIN, HIGH);
  digitalWrite(TBPOWERPIN, HIGH);
  
  if(homeSorterOnStartup){
       checkSorterHoming(false);
  }
  if(homeFeedOnStartup){
      checkFeedHoming(false);
  }

  Serial.print("Ready\n");
}

void loop() {

  if (Serial.available() > 0) {

    String input = Serial.readStringUntil('\n');

    //normal input would just be the tray # you want to sort to which would be something like "1\n" or "9\n" (\n)if you are using serial console, the \n is already included in the writeline
    //so just the number 1-10 would suffice.
    //the software on the other end should be listening for  "done\n".

    //if true was returned, we go to next looping, else we continue down below
    if (parseSerialInput(input) == true) {
      return;
    }

    int sortPosition = input.toInt();
    QueueAdd(sortPosition);



    runSorterMotor(QueueFetch());

    runFeedMotorManual();
    checkFeedHoming(true);
    feedDone();
    delay(30);  //allow for vibrations to calm down for clear picture
    Serial.print("done\n");
    PrintQueue();
  }
  delay(1);
}


//These are the commands to execute when feed is done
void feedDone() {
    digitalWrite(FEED_DONE_SIGNAL, HIGH);
    delay(feedDoneSignalTime);
    digitalWrite(FEED_DONE_SIGNAL,LOW);
}

void checkFeedHoming(bool isAutoHomeCycle) {
  if (isAutoHomeCycle == true && autoFeedHoming == false)
    return;

  int homingSensorVal = digitalRead(FEED_HOMING_SENSOR);

  if (homingSensorVal == 1) {
    return;  //we are homed! Continue
  }

  int i = 0;  //safety valve..
  int offset = homingFeedOffset * FEED_MICROSTEPS;
  while ((homingSensorVal == 0 && i < 12000) || offset > 0) {
    runFeedMotor(1);
    homingSensorVal = digitalRead(FEED_HOMING_SENSOR);
    i++;
    if (homingSensorVal == 1) {
      offset--;
    }
  }
}

void checkSorterHoming(bool isAutoHomeCycle) {
  if (isAutoHomeCycle == true && autoSorterHoming == false)
    return;

  int homingSensorVal = digitalRead(SORT_HOMING_SENSOR);
  //Serial.println(homingSensorVal);

  int offset = homingSortOffset * FEED_MICROSTEPS;

  //if we are triggering the sensor and isAutoHomeCycle is not true, we run the motor forward a few steps and home back slowely
  //This does the jump. But if isAutoHomeCycle is false, the we just need to run the offset and are back off to the races.
  if (homingSensorVal == 1 && isAutoHomeCycle == false) {
    int hfs = 15 * SORT_MICROSTEPS;
    runSortMotorManual(hfs);
  } else if (homingSensorVal == 1) {
    runSortMotorManual(offset);
    return;
  }

    //when trying to find home, the sorter arm should not move more than one full rotation (200 steps)
    int homingMax = 198 * FEED_MICROSTEPS;
    while (digitalRead(SORT_HOMING_SENSOR) == 0 && homingMax > 0) {
      runSortMotorManual(-1);
      homingSensorVal = digitalRead(FEED_HOMING_SENSOR);
      homingMax--;
    }

    //now lets run forward our offset
    runSortMotorManual(offset);

}

//moves the sorter arm. Blocking operation until complete
void runSorterMotor(int chute) {
  //you can uncomment to use the array sorterChutes for exact positions of each slot
  //int newStepsPos = sorterChutes[chute]; //the steps position from zero of the "slot"

  //rather than use exact positions, we are assuming uniform seperation betweeen slots specified by sorter_chute_seperation constant
  int newStepsPos = chute * SORTER_CHUTE_SEPERATION;

  //calculate the amount of movement and move.
  int nextmovement = newStepsPos - sorterMotorCurrentPosition;  //the number of +-steps between current position and next position
  int movement = nextmovement * SORT_MICROSTEPS;                //calculate the number of microsteps required

  if (movement != 0) {
    delay(slotDropDelay);
  }

  if (useAcceleration) {
    runSortMotorManualAcc(movement);
  } else {
    runSortMotorManual(movement);
  }

  //if the chute command is zero and we were not already at zero, we autohome if enabled
  if(chute==0 && abs(movement) > 0){
    checkSorterHoming(true); 
  }

  sorterMotorCurrentPosition = newStepsPos;
}

void runFeedMotorManual() {

  if (useFeedSensor) {
    int i = 0;
    while (digitalRead(FEED_SENSOR) != 0) {
      i++;
      delay(10);
      if (i == 200) {
        Serial.println("Waiting for brass");
        i=0;
      }
      if (Serial.available() > 0) {
        String input = Serial.readStringUntil('\n');
        if (parseSerialInput(input) == false) {
          break;
        }
      }
      if(i>10000){
         i=0;
      }
    }
  }
  int steps = 0;

 
  digitalWrite(FEED_DIRPIN, LOW);
  int curFeedSteps = abs(feedSteps);
  //calculate the steps based on microsteps.
  steps = curFeedSteps * FEED_MICROSTEPS;

  for (int i = 0; i < steps; i++) {
    digitalWrite(FEED_STEPPIN, HIGH);
    delayMicroseconds(pulsewidth);  //pulse. recommended minimum > than 1 micro
    digitalWrite(FEED_STEPPIN, LOW);
    delayMicroseconds(feedMotorSpeed);
  }
}

void runFeedMotor(int steps) {
  digitalWrite(FEED_DIRPIN, LOW);
  for (int i = 0; i < steps; i++) {
    digitalWrite(FEED_STEPPIN, HIGH);
    delayMicroseconds(pulsewidth);  //pulse. i have found 60 to be very consistent with tb6600. Noticed that faster pulses tend to drop steps.
    digitalWrite(FEED_STEPPIN, LOW);
    delayMicroseconds(feedMotorSpeed);  //speed 156 = 1 second per revolution
  }
}

void runSortMotorManual(int steps) {

  if (steps > 0) {
    digitalWrite(SORT_DIRPIN, LOW);
  } else {
    digitalWrite(SORT_DIRPIN, HIGH);
  }
   delayMicroseconds(10);
  steps = abs(steps);
  for (int i = 0; i < steps; i++) {
    digitalWrite(SORT_STEPPIN, HIGH);
    delayMicroseconds(pulsewidth);  //pulse //def 60
    digitalWrite(SORT_STEPPIN, LOW);
    delayMicroseconds(sorterMotorSpeed);  //speed 156 = 1 second per revolution //def 20
  }
}

void runSortMotorManualAcc(int steps) {

  if (steps == 0)
    return;
  bool forward = true;
  if (steps > 0) {
    digitalWrite(SORT_DIRPIN, LOW);
  } else {
    digitalWrite(SORT_DIRPIN, HIGH);
    forward = false;
  }
  delay(5);

  steps = abs(steps);

  int fullspeedsteps = steps - downslope - upslope;
  //accelerate linear
  for (int i = 1; i <= upslope; i++) {

    int msdelay = accelerationFactor - (i * rampFactor);
    if (msdelay < sorterMotorSpeed) {
      msdelay = sorterMotorSpeed;
    }
    digitalWrite(SORT_STEPPIN, HIGH);
    delayMicroseconds(pulsewidth);  //pulse //def 60
    digitalWrite(SORT_STEPPIN, LOW);
    delayMicroseconds(msdelay);  //speed 156 = 1 second per revolution //def 20
  }

  //full speed
  for (int i = 1; i <= fullspeedsteps; i++) {
    digitalWrite(SORT_STEPPIN, HIGH);
    delayMicroseconds(pulsewidth);  //pulse //def 60
    digitalWrite(SORT_STEPPIN, LOW);
    delayMicroseconds(sorterMotorSpeed);  //speed 156 = 1 second per revolution //def 20
  }

  //Deaccelerate linear
  for (int i = 1; i <= downslope; i++) {
    int msdelay = sorterMotorSpeed + (i * rampFactor);
    if (msdelay >= sorterMotorSpeed) {
      msdelay = accelerationFactor;
    }
    digitalWrite(SORT_STEPPIN, HIGH);
    delayMicroseconds(pulsewidth);  //pulse //def 60
    digitalWrite(SORT_STEPPIN, LOW);
    delayMicroseconds(msdelay);  //speed 156 = 1 second per revolution //def 20
  }
}


void setSorterMotorSpeed(int speed) {
  sorterMotorSpeed = setSpeedConversion(speed);
}
void setFeedMotorSpeed(int speed) {
  feedMotorSpeed = setSpeedConversion(speed);
}

int setSpeedConversion(int speed) {
  if (speed < 1 || speed > 100) {
    return 500;
  }
  double proportion = (double)(speed - 1) / 99;       //scale the range to number between 0 and 1;
  int output = (int)(proportion * (1000 - 60)) + 60;  //scale range 0-1 to desired output range
  int finaloutput = 1060 - output;  //reverse the output;
  return finaloutput;
}


//used for debugging queue issues.
void PrintQueue() {
  if (PRINT_QUEUEINFO == false)
    return;
  Serial.print("-------\n");
  Serial.print("QueueStatus:\n");
  for (int i = 0; i < QUEUE_LENGTH; i++) {
    if (i > 0)
      Serial.print(',');
    Serial.print(sorterQueue[i]);
  }
  Serial.print("\nSorting to: ");
  Serial.print(QueueFetch());
  Serial.print("\n-------\n");
}

//adds a position item into the front of the sorting queue. Queue is used in FIFO mode. PUSH
void QueueAdd(int pos) {
  for (int i = QUEUE_LENGTH; i > 0; i--) {
    sorterQueue[i] = sorterQueue[i - 1];
  }
  sorterQueue[0] = pos;
}

//fetches items from back of queue. POP
int QueueFetch() {
  return sorterQueue[QUEUE_LENGTH - 1];
}

//return true if you wish to stop processing and continue to next loop
bool parseSerialInput(String input) {
  if (isDigit(input[0])) {
    return false;
  }
 
 if (input.startsWith("xf:")) {
    input.replace("xf:", "");
    int sortPosition = input.toInt();
    QueueAdd(sortPosition);
    runSorterMotor(QueueFetch());
     useFeedSensor = false;
    runFeedMotorManual();
    checkFeedHoming(true);
    feedDone();
    useFeedSensor = FEEDSENSOR_ENABLED;
    delay(20);  //allow for vibrations to calm down for clear picture
    Serial.print("done\n");
    return true;
  }

  if (input.startsWith("usefeedsensor:")) {
    input.replace("usefeedsensor:", "");
    useFeedSensor = false;
    if (input == "1") {
      useFeedSensor = FEEDSENSOR_ENABLED;
    }
    Serial.print("ok\n");
    return true;
  }
  //set feed speed. Values 1-100. Def 60
  if (input.startsWith("feedspeed:")) {
    input.replace("feedspeed:", "");
    feedSpeed = input.toInt();
    setFeedMotorSpeed(feedSpeed);
    Serial.print("ok\n");
    return true;
  }

 if (input.startsWith("feeddone")) {
    feedDone();
    Serial.print("ok\n");
    return true;
  }

  //used to test tracking on steppers for feed motor. specify the number of feeds to perform: eg:  "test:60" will feed 60 times.
  if (input.startsWith("test:")) {
    input.replace("test:", "");
    int testcount = input.toInt();
    int slot = 0;
    for (int a = 0; a < testcount; a++) {
      slot = random(0, 5);
      Serial.print(a);
      Serial.print(" - ");
      Serial.print(slot);
      runSorterMotor(slot);
      runFeedMotorManual();
      checkFeedHoming(true);
      feedDone();
      Serial.print("\n");
      delay(sortTestDelay);
    }
    Serial.print("ok\n");
    return true;
  }

  //used to test tracking on steppers for feed motor. specify the number of feeds to perform: eg:  "test:60" will feed 60 times.
  if (input.startsWith("sorttest:")) {
    input.replace("sorttest:", "");
    int testcount = input.toInt();
    int slot = 0;
    int cslot = 0;

    for (int a = 0; a <= testcount; a++) {
      if (a == testcount) {
        runSorterMotor(0);
        continue;
      }

      slot = random(0, 7);
      while (slot == cslot) {
        slot = random(0, 6);
      }

      cslot = slot;
      Serial.print(a);
      Serial.print(" - ");
      Serial.print(slot);
      Serial.print("\n");
      runSorterMotor(slot);
      delay(sortTestDelay);
    }


    runSorterMotor(0);
    Serial.print("ok\n");
    return true;
  }

  //set sort speed. Values 1-100. Def 60
  if (input.startsWith("sortspeed:")) {
    input.replace("sortspeed:", "");
    sortSpeed = input.toInt();
    setSorterMotorSpeed(sortSpeed);
    Serial.print("ok\n");
    return true;
  }

  //set sort steps. Values 1-100. Def 20
  if (input.startsWith("sortsteps:")) {
    input.replace("sortsteps:", "");
    sortSteps = input.toInt();
    Serial.print("ok\n");
    return true;
  }

  //set feed steps. Values 1-1000. Def 100
  if (input.startsWith("feedsteps:")) {
    input.replace("feedsteps:", "");
    feedSteps = input.toInt();
    Serial.print("ok\n");
    return true;
  }


  //set feed steps. Values 1-1000. Def 100
  if (input.startsWith("autohome:")) {
    input.replace("autohome:", "");
    input.replace(" ", "");
    autoFeedHoming = input == "1";
    Serial.print("ok\n");
    return true;
  }

  //to change sorter arm position by slot number
  if (input.startsWith("sortto:")) {
    input.replace("sortto:", "");
    int msortsteps = input.toInt();
    runSorterMotor(msortsteps);
    Serial.print("done\n");
    return true;
  }

  //to change sorter arm position by steps.
  if (input.startsWith("sorttosteps:")) {
    input.replace("sorttosteps:", "");
    int msortsteps = input.toInt();
    runSortMotorManual(msortsteps);
    Serial.print("done\n");
    return true;
  }

  //home the feeder
  if (input.startsWith("homefeeder")) {
    checkFeedHoming(false);
    Serial.print("done\n");
    return true;
  }

  if (input.startsWith("homesorter")) {
    checkSorterHoming(false);
    Serial.print("done\n");
    return true;
  }

  if (input.startsWith("getconfig")) {

    Serial.print("{\"FeedMotorSpeed\":");
    Serial.print(feedSpeed);

    Serial.print(",\"FeedCycleSteps\":");
    Serial.print(feedSteps);

    Serial.print(",\"SortMotorSpeed\":");
    Serial.print(sortSpeed);

    Serial.print(",\"SortSteps\":");
    Serial.print(sortSteps);

    Serial.print("}\n");
    return true;
  }

  return false;  //nothing matched, continue processing the loop at normal
}

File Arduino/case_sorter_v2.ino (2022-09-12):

#include <AccelStepper.h>
#include <Wire.h>
#include <SoftwareSerial.h>


//TB6600 PINS (STEPPIN IS PUL+ ON TB6000)
//Stepper controller is set to 32 Microsteps
#define FEED_DIRPIN 8
#define FEED_STEPPIN 9
#define FEED_TB6600Enable 2
#define FEED_MICROSTEPS 32


#define SORT_MICROSTEPS 32 
#define SORT_DIRPIN 5
#define SORT_STEPPIN 6
#define SORT_TB6600Enable 4

#define SORTER_CHUTE_SEPERATION 20 //number of steps between chutes

//motor movement settings for feeder
int indexSteps = 5;
int microSteps = 1;
int feedCycleSteps = indexSteps * FEED_MICROSTEPS * -1;


int sorterMotorCurrentPosition = 0;
int sorterChutes[] ={0,17, 33, 49, 66, 83, 99, 116, 132}; 


void setup() {
  Serial.begin(9600);
  pinMode(FEED_TB6600Enable, OUTPUT);
  pinMode(SORT_TB6600Enable, OUTPUT);
  digitalWrite(FEED_TB6600Enable, LOW);
  digitalWrite(SORT_TB6600Enable, LOW);

}

void loop() {

    if(Serial.available() > 0 )  
    {
      
      String input = Serial.readStringUntil('\n');
      
      //normal input would just be the tray # you want to sort to which would be something like "1\n" or "9\n" (\n)if you are using serial console, the \n is already included in the writeline
      //so just the number 1-10 would suffice. 

     //the software on the other end should be listening for  "done\n". 
     
      if(input.startsWith("fs")){
         input.replace("fs","");
         indexSteps= input.toInt();
         feedCycleSteps = indexSteps * FEED_MICROSTEPS * -1;
         return;
      }

      //to change sorter arm position, send x1, x2.. x10, etc. 
      if(input.startsWith("x")){
         input.replace("x","");
         int msortsteps= input.toInt();
         //runSorterMotorSteps(msortsteps);
         runSortMotorManual(msortsteps);
         Serial.print("done\n");
         return;
      }
      
      //too run feeder, send  any string starting with f:
       if(input.startsWith("f")){
         input.replace("f","");
         runFeedMotorManual();
         Serial.print("done\n");
         return;
      }
      

      
      int sortPosition = input.toInt();
      runSorterMotor(sortPosition);
      runFeedMotorManual();
      delay(100);//allow for vibrations to calm down for clear picture
      Serial.print("done\n");
    }

}

//moves the sorter arm. Blocking operation until complete
void runSorterMotor(int chute){

   //int newStepsPos = sorterChutes[chute]; //the steps position from zero of the "slot"
   
   int newStepsPos = chute * SORTER_CHUTE_SEPERATION;
   int nextmovement = newStepsPos - sorterMotorCurrentPosition; //the number of +-steps between current position and next position
   int movement = nextmovement * SORT_MICROSTEPS; //calculate the number of microsteps required
   
   runSortMotorManual(movement);
   sorterMotorCurrentPosition = newStepsPos;
}


void runFeedMotorManual(){
  int steps=100;
  digitalWrite(FEED_DIRPIN, HIGH);
  steps = abs(steps) * FEED_MICROSTEPS;
  for(int i=0;i<steps;i++){
      digitalWrite(FEED_STEPPIN, HIGH);
      delayMicroseconds(60);   //pulse
      digitalWrite(FEED_STEPPIN, LOW);
      delayMicroseconds(20); //speed 156 = 1 second per revolution
  }
  delay(50);
  for(int i=0;i<steps;i++){
      digitalWrite(FEED_STEPPIN, HIGH);
      delayMicroseconds(60);   //pulse
      digitalWrite(FEED_STEPPIN, LOW);
      delayMicroseconds(20); //speed 156 = 1 second per revolution
  }
  //Serial.print(steps);Serial.print("\n");
}


void runSortMotorManual(int steps){
  if(steps>0){
    digitalWrite(SORT_DIRPIN, HIGH);
  }else{
    digitalWrite(SORT_DIRPIN, LOW);
  }
  steps = abs(steps) ;
  for(int i=0;i<steps;i++){
      digitalWrite(SORT_STEPPIN, HIGH);
      delayMicroseconds(60);   //pulse
      digitalWrite(SORT_STEPPIN, LOW);
      delayMicroseconds(20); //speed 156 = 1 second per revolution
  }
  //Serial.print(steps);Serial.print("\n");
}

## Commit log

2022-09-12 Added top level feeder 3d print resources
    [CS6_Complete.stl]
2022-09-12 Added arduino code and additional models
    [CS5_CameraModule.stl, CS5_LightRing.stl, CS5_PVC_PLATE.stl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]
2022-09-13 Added Individual Modules
    [CS6_223FeedPiston.stl, CS6_9mmFeedFunnel.stl, CS6_Con-rod.stl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]
2022-09-14 Updates for camera module and threaded feed piston
    [CS5_CameraModule.stl, CS6_CameraBody.stl, CS6_Complete.stl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]
2022-09-25 updated models
    [CS5_CameraModule.stl, CS5_CameraModule_Lid.stl, CS5_CameraModule_lid_flat.stl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]
2022-10-02 fixed bug for 36 ms added queue
    [case_sorter_v2.ino]
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2022-10-10 added sliced and cura project
    [CFFFP_CS6_Complete.3mf]
2022-10-14 Added CS7 Versions
    [CS7_223-556-IndexWheel.stl, CS7_9mm-IndexWheel.stl, CS7_BlackBox_Base.stl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]
2022-10-14 moved 3d assets to version dir
    [CFFFP_CS6_Complete.3mf, CS5_CameraModule.stl, CS5_CameraModule_Lid.stl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]
2022-10-14 added auto homing
    [SorterBin.stl]
2022-10-16 Added New LId Models
    [BlackBox Lid Screw Version.stl, Blackbox Lid Clippy Version.stl, CS7_BlackBox_Base_wSensor.stl]
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2022-10-31 added 45 stuff
    [CS7-45AUTO-Conversion.stl, CS7-Wheel-45AUTO.stl, CS7_BlackBox_Base.stl]
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2022-11-09 Added 308 resources
    [BlackBox Lid Screw Version_V2_tall.stl, CS7-308-Conversion.stl, CS7-45SortNozzle.stl]
2022-11-11 Updated the models for base and nozzles
    [CS7_9mm_Feed_nozzle.stl, CS7_9mm_nozzle.stl, CS7_BlackBox_Base.stl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]
2022-11-12 added new sorter pipe set
    [NewSortPipeSet.stl, SplitPipe_Bottom.stl, SplitPipe_Top.stl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]
2022-11-12 fixed spelling...
    [NewSortPipeSet.stl, SplitPipe_Bottom.stl, SplitPipe_Top.stl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]
2022-11-17 Reorganized and expanded readme's
    I reorganized the files into modules and sorted them all out so that it is easier to understand how to replicate the project.
    I sorted out the versions and intend to ensure that all versions have all the required parts included and documented.
    Added modules readme's
    [BlackBox Lid Screw Version(Archived due to height incompatability).stl, Blackbox Lid Clippy Version(Archived due to height incompatability).stl, CFFFP_CS6_Comp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]
2022-11-17 Added nameplate to sorter bins
    [SortingBin.stl]
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2022-11-18 added minimal sort plate
    modified the sort plate to what I believe to be the minimum viable solution. I removed all of the sort pipe holes and added indexing notches so that position calibration can still be done. This is fo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
    [minimal sort plate v1.stl]
2022-11-20 Update CS7_Classifier_Lid.stl
    Opened up the feed side of the classifier lid to provide more visibility to allow for better adjustment of the feed tube
    [CS7_Classifier_Lid.stl]
2022-11-21 Added new sorter minimal design to experimental folder
    [SorterMinimalDesign.stl, SorterMinimalDesign_MotorSide.stl, SorterMinimalDesign_PoleSide.stl]
2022-11-28 Update CS7_Camera_Nut.stl
    Fixed the camera nut issue identified in https://github.com/sjseth/AI-Case-Sorter/issues/8#issue-1465418649
    I had induced this issue while breaking the parts out of the combined file and it was committed in 0ed8f6243957939c9040e33a33dbda119ad291d2
    [CS7_Camera_Nut.stl]
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2022-11-29 Added experimental enclosure for uno with motorshield
    [CS7 - Arduino Uno Shield Enclosure.stl, CS7 - Arduino Uno Shield Enclosure_Bottom.stl, CS7 - Arduino Uno Shield Enclosure_Lid.stl]
2022-12-03 Updated enclosure to make a little larger for fat fingers
    [CS7 - Arduino Uno Shield Enclosure Project.3mf, CS7 - Arduino Uno Shield Enclosure.stl, CS7 - Arduino Uno Shield Enclosure_Bottom.stl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]
2022-12-05 Electronics housing for Arduino Nano Every + TB6600
    Made a housing for the electronics. Seems your moving away from these components, but I'll still upload it for your review.
    [CS7 - Nano + TB6600 Electronics Lid.stl, CS7 - Nano + TB6600 Electronics Main.stl]
2022-12-05 Updated Drive Gear to shorten it to prevent interference
    [CS7 Camera v2.stl, CS7_Classifier_Drive_Gear.stl]
2022-12-05 Added for Issue #16
    [CS7 - Feed Adaptor - B556.stl]
2022-12-06 Fixed drive gear and recessed screws
    Drive gear was upside down and needed to be flipped so no supports required during printing.
    Recessed screws on base to prevent interference
    [CS7_Classifier_Base.stl, CS7_Classifier_Complete.stl, CS7_Classifier_Drive_Gear.stl]
2022-12-07 update b556 feed adaptor to 17mm for issue #17
    [CS7 - Feed Adaptor - B556.stl, CS7 Camera v2.stl]
2022-12-09 Update CS7_Thumbscrew_M3.stl
    Better knurling, for better grip.
    These are pushfit, no glue required.
    [CS7_Thumbscrew_M3.stl]
2022-12-10 Create CS7 - 9mm Drop Nozzle.stl
    [CS7 - 9mm Drop Nozzle.stl]
2022-12-10 Organized enclosure assets
    [CS7 - Arduino Uno Shield Enclosure Project.3mf, CS7 - Arduino Uno Shield Enclosure.stl, CS7 - Arduino Uno Shield Enclosure_Bottom.stl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]
2022-12-11 Added updated model with jack holes moved 5mm
    [CS7 - Arduino Uno Shield Enclosure Project.3mf, CS7 - Arduino Uno Shield Enclosure.stl, CS7 - Arduino Uno Shield Enclosure_Bottom.stl]
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2022-12-16 Create CS7 - Arduino Uno Shield Enclosure_Bottom-22mm_pwr_btn-pole_mount.stl
    Added a modified version of the uno enclosure that uses 22mm power buttons that I had on hand.
    Additionaly, I added mounting holes so that his box can be mounted to the collator pole using a second printing of the the SorterMinimalDesign as the mount.
    [CS7 - Arduino Uno Shield Enclosure_Bottom-22mm_pwr_btn-pole_mount.stl]
2022-12-18 Create 11mm_Power_plug_grommet.stl
    I had 11mm power plugs on hand and made a small grommet to size the hole down. Method of use it to print 2, push 1 into the power plug hole from each side to size the existing hole down and then inst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
    [11mm_Power_plug_grommet.stl]
2022-12-22 Added some new experimental items for fixing issues where brass falls into camera hole
    [CFFFP_CS7 - Sorter Base Exp.3mf, CS7 - SlopRemovalNut.stl, CS7 - Sorter Base Exp.stl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]
2022-12-25 fixed bugs in arduino code
    [case_sorter_CS7.ino, case_sorter_CS7_UNOSHIELD.ino, case_sorter_v2.ino]
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2023-01-16 Added 27mm mounts
    To support using the larger 1in iron pipe, these mounts have ID of 27.6mm.
    [CS7 Classifier Mount_27mm.stl, SORTER_PLATEPOLEMOUNT_27mm.stl]
2023-01-16 added 27mm mount for minimal sorter
    Allows people to use iron pipe 3/4 which has od of 26.7mm
    [Sorter Minimal Mount_27mm.stl]
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2023-02-07 fixed bug in homing method
    [case_sorter_CS7.ino]
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2023-02-11 added delay to fix blurred images
    [case_sorter_CS7_UNOSHIELD.ino]
2023-02-18 fixed issue with motor speed
    [case_sorter_CS7.ino, case_sorter_CS7_UNOSHIELD.ino]
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
